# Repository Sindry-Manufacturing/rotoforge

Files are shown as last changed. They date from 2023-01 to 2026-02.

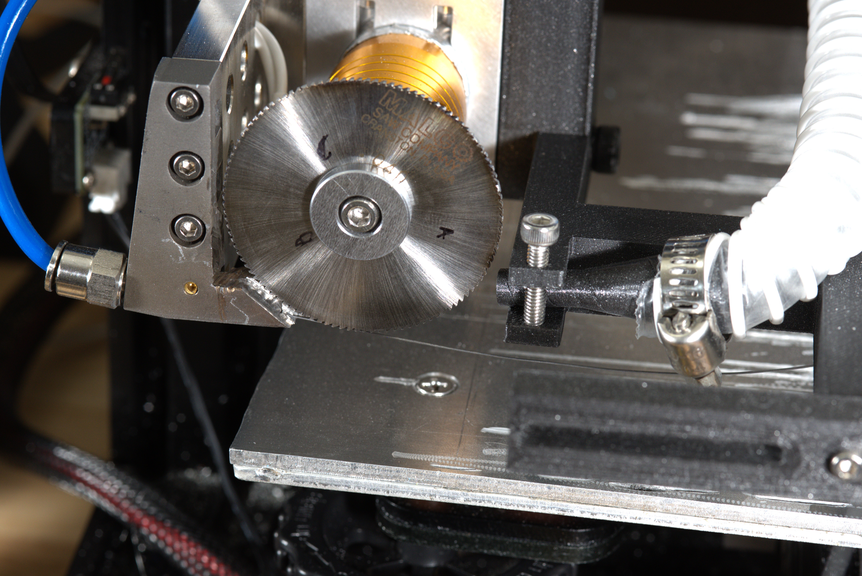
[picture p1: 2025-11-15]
docs/img/DSC_7158.jpg

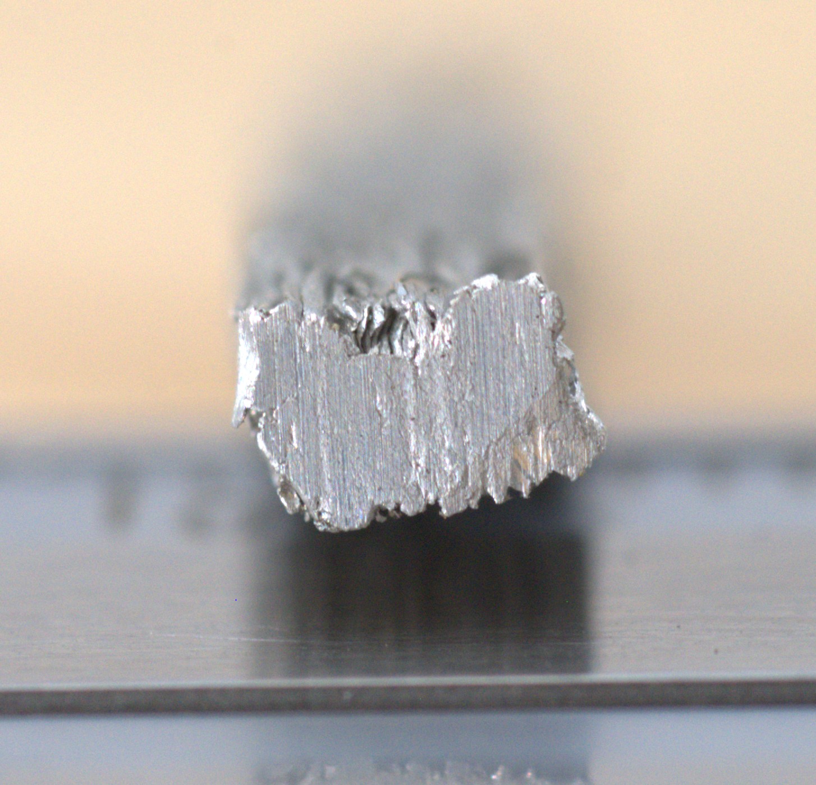
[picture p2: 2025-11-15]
docs/img/firstcleanal1100depositgroundsection.jpg

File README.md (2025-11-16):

# Rotoforge README
picture of first working iteration of Rotoforge to print a 10 mm tall wall with Al1100 wire

This is  **Rotoforge**, a 3D printer that uses continuous [friction welding](https://en.wikipedia.org/wiki/Friction_welding) to print metals, plastics and ceramics heterogeneously. 
If a wire is fed into the contact patch of a [wheel](https://en.wikipedia.org/wiki/Wheel_and_axle) which is spinning fast enough and with sufficient torque, the wire will heat up due to [friction](https://en.wikipedia.org/wiki/Friction), and become more flowable(see [thixotropy](https://en.wikipedia.org/wiki/Thixotropy)) due to plastic shear(see [flow stress](https://en.wikipedia.org/wiki/Flow_stress) and the [Zener-Hollomon Parameter](https://en.wikipedia.org/wiki/Zener%E2%80%93Hollomon_parameter)). 

Under these conditions, even materials like aluminum, copper, steel, glass, and high grade engineering plastics will become extremely fluid (without melting) and bond (given the correct contact and mixing conditions) at the contact patch, in air, without a [shield gas](https://en.wikipedia.org/wiki/Shielding_gas)!, at relatively low temperatures  and pressures. This allows relatively low force, FDM like printing of these materials on a standard 3D printer, given a way to feed wire, and a wheel with adequate speed and torque to keep the material flowing under the chosen RPM and feed rate conditions. 
This printing process, like [forging](https://en.wikipedia.org/wiki/Forging), can yield material which is stronger as printed, than the initial feedstock.  

For example, when printing with Al1100 from full soft [wire](https://www.mcmaster.com/8904k47/) (yield tensile strength (YTS) ~25 MPa, ultimate tensile strength (UTS) ~90 MPa at 100% elongation) Rotoforge achieves ~90 MPa YTS and ~120 MPa UTS at 33% elongation. a 3.6X and 1.5X improvement respectively at a modest cost in ductility. (approximate equivalent to printing ~H18 temper Al-1100)

Here is what I recommend for [getting started with Rotoforge](https://github.com/Sindry-Manufacturing/rotoforge/blob/7352ae5f737d98ba2852f8fd07662a8f5acfcd73/docs/getting_started/Getting_Started/getting_started.md)

If you would like to download the part files, schematics and documentation including text assembly tutorials and a getting started guide, clone the repository, or download the zipped folder here on github. 
We also have a [youtube channel](https://www.youtube.com/channel/UCBE1bfTLnz7WSu8h5rG6ihA) and a [read the docs page](https://www.rotoforge.com/introduction/).

If you want regular updates on progress from Michael, he has a [blog](https://dailyrotoforge.blogspot.com/) he updates periodically. 

For more active discussions we have a [discord channel](https://discord.gg/T6tJYQXE26) and a subreddit. 

for proper data storage on feeds and speeds and other printing and deposition parameters as well as in process data storage we have a [zenodo repository:](https://zenodo.org/records/10365783)

and we are occasionally active on the GOSH [community forums:](https://forum.openhardware.science/t/rotoforge-an-affordable-open-source-multimaterial-3d-printer-for-printing-metal-plastic-and-ceramics-on-the-home-desktop/4570/11)

# Files

Included in this Rotoforge repository are:
[a bill of materials](https://github.com/Sindry-Manufacturing/rotoforge/blob/5657fceeaa8cc7267cb5c8fe33cddc3ae800ea73/docs/billsofmaterials),for sourcing your own parts,

[guidelines for contributing](https://github.com/Sindry-Manufacturing/rotoforge/blob/5657fceeaa8cc7267cb5c8fe33cddc3ae800ea73/contributionguidelines.md) for those looking to be part of the community,
and 
[Documentation files](https://github.com/Sindry-Manufacturing/rotoforge/blob/5657fceeaa8cc7267cb5c8fe33cddc3ae800ea73/docs) to get the new user/developer started and provide some basic guidance for troubleshooting.

Source files, [including complete CAD data for the mechanical parts](https://github.com/Sindry-Manufacturing/rotoforge/blob/5657fceeaa8cc7267cb5c8fe33cddc3ae800ea73/src/parts/CAD), and electronics and source code to build and operate your own Rotoforge on an Ender 3 motion platform.  Principally rotoforge can be built on any motion platform, and more rigidity is better, but not strictly neccessary.
Also a [small cache of untested](https://github.com/Sindry-Manufacturing/rotoforge/blob/5657fceeaa8cc7267cb5c8fe33cddc3ae800ea73/untested%20designs) desgins in the works by other developers.

## Mechanical Parts
Rotoforge is currently just a mechanical and electronics attachment for an FDM printer which enables continuous friction welding as the new mode of energy injection and material deposition. the original mechanical CAD files are native to **Fusion360**. 
I intend to provide OpenSCAD or similar fully open source versions in the future. 

## Electronic parts
Rotoforge electronics are modeled in KiCAD and EaglePCB.  There are off the shelf versions available as well that do the job. Mostly you will need:
In the US: a 110->240 volt step up transformer.
a Variac or other method to control the speed of the flex shaft grinder (not required but useful).
A >800 watt flex shaft grinder(sometimes called a "rotary tool" or "flexshaft die grinder").

## Software
There is presently only [simple demo software for Rotoforge](https://github.com/Sindry-Manufacturing/rotoforge/blob/5657fceeaa8cc7267cb5c8fe33cddc3ae800ea73/src/afrb_playground_gui(2).py), as it runs on the motion control code and firmware of a typical FDM machine. All you will need to do to start exploring is install the mechanical and electronic parts, and use your slicer of choice (or use my provided python g-code generator) to adjust your feeds and speeds to suit the requirements of printing metals, plastics and potentially ceramics of your choice. **There is currently very little information in the wild on what feeds and speeds will work so this is a big point of ongoing exploration and where almost anyone could help!**  

## The Future
The printer only drives in straight lines in -X direction (it has to reset after every line to build thickness in Z) and can print while drifting at up to ~+-30 degree angles in the  direction right now. Typical deposition rates are 4-12 mm^3/s in this mode. But soon with the addition of a 4th axis and closed loop spindle and deposition temperature controls we will be printing ironclad boats, rocket, and car engines, robot, bicycle and car parts, at 2-4X faster in strong aluminum, copper, steel, and with your help beyond!

Rotoforge software is licensed under the [AGPL-V3](https://www.gnu.org/licenses/agpl-3.0.en.html)

Rotoforge hardware is licensed under the [CERN Open Hardware License-strong](https://cern-ohl.web.cern.ch/)

There is a video assembly guide for this printer modification [here](https://www.youtube.com/watch?v=yMjR5zOKrdI&t=20s&ab_channel=Rotoforge)
There are ongoing blogs and technical details on development of the hardware, physics and materials science involved in this project [here](https://dailyrotoforge.blogspot.com/)

## Safety
**This printer mod is LOUD and can create high speed flying debris (the wheel at full speed stores as much energy as a .357 magnum bullet). Wear eye/face/body/ear protection while the printer is in operation. If you choose not to do this, I would recommend enclosing the printer to protect you and your property and family.  If you choose to operate the printer without these safety measures, you do so at your own risk.**

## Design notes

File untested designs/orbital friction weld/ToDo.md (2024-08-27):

# To Do
- add wiring hole for motor
- add prices to BOM
- add features to mount to printer
- add large bearing in BOM
- name parts in model

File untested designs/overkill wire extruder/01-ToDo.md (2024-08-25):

# To Do
- update BOM with skrews m3 and m6
- add shaft cut list
- machin        e and test rollers

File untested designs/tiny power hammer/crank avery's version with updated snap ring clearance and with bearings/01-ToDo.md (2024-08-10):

# To Do
- update BOM with skrews
- add linear rail to BOM

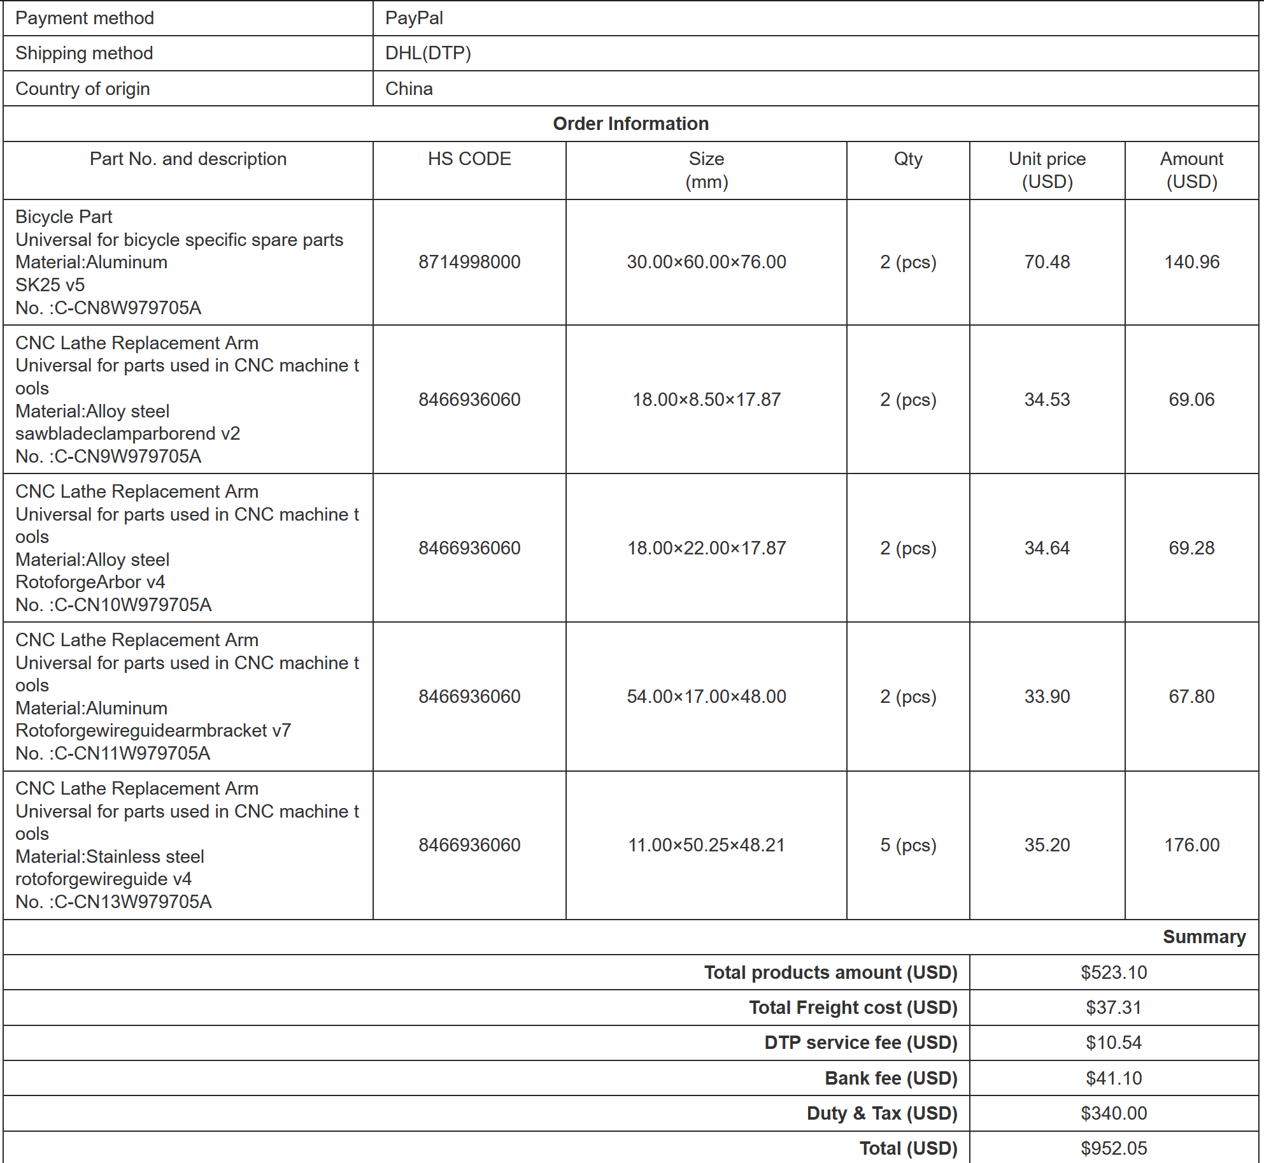
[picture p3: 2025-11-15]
docs/img/costofmechanicalpartsfromPCBway.png

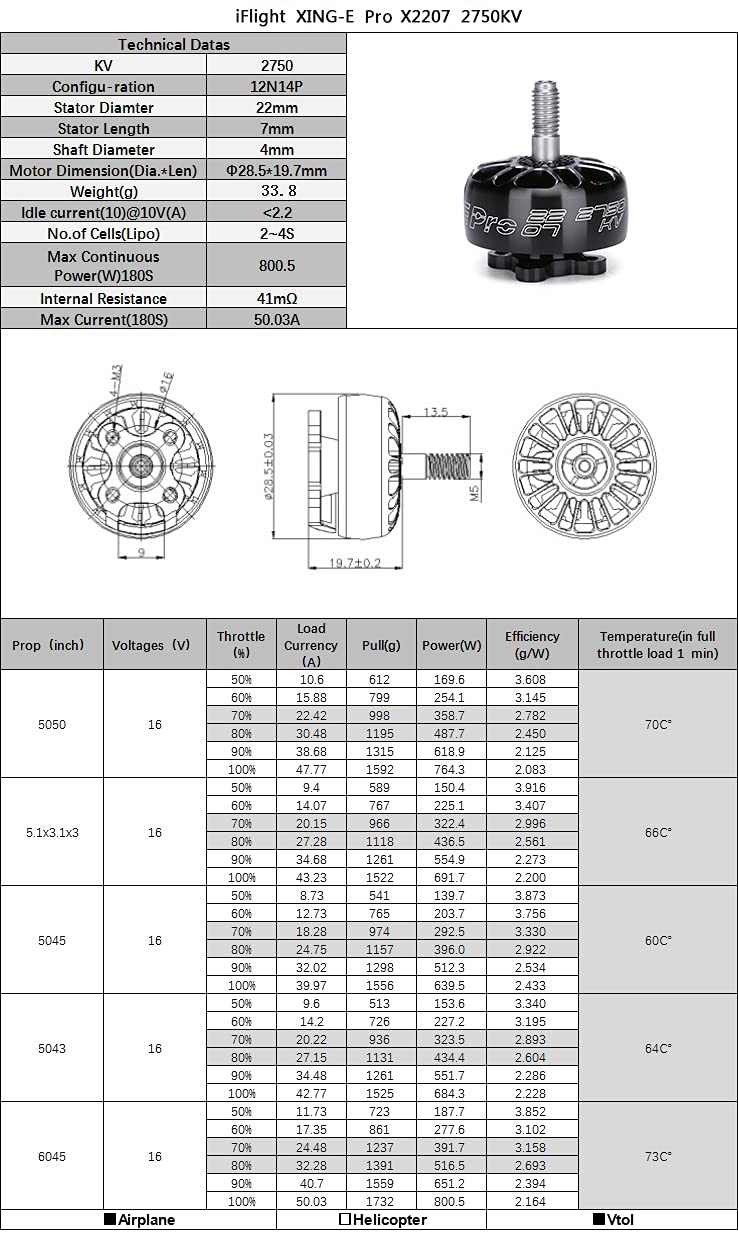
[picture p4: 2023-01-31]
src/parts/Schematics/xingEflightpro2207_.jpg

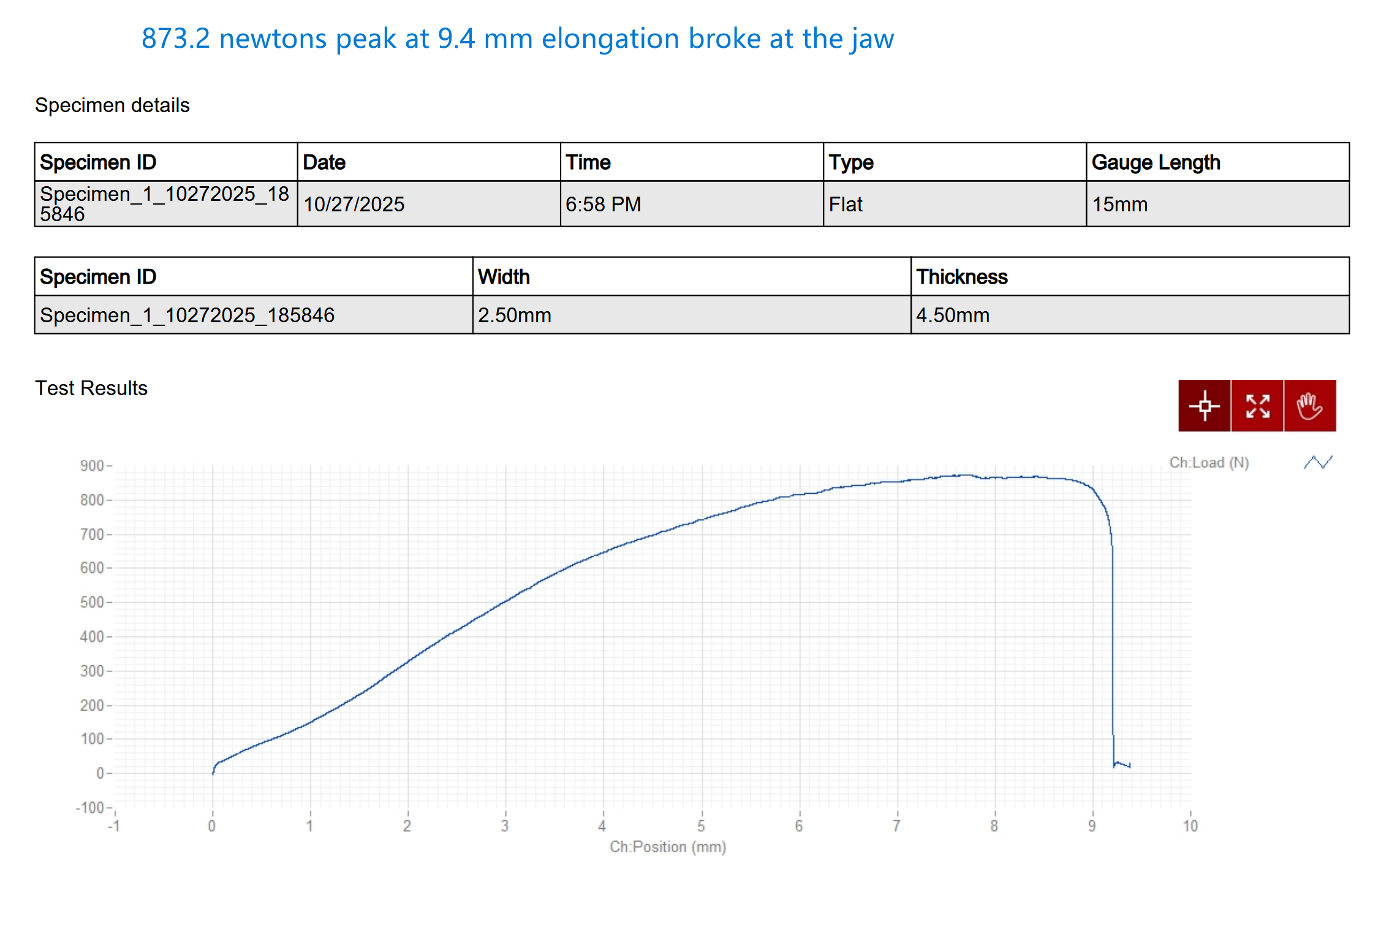
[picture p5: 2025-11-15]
docs/img/al1100asprintedtensiletest2Screenshot 2025-11-15 150118.png

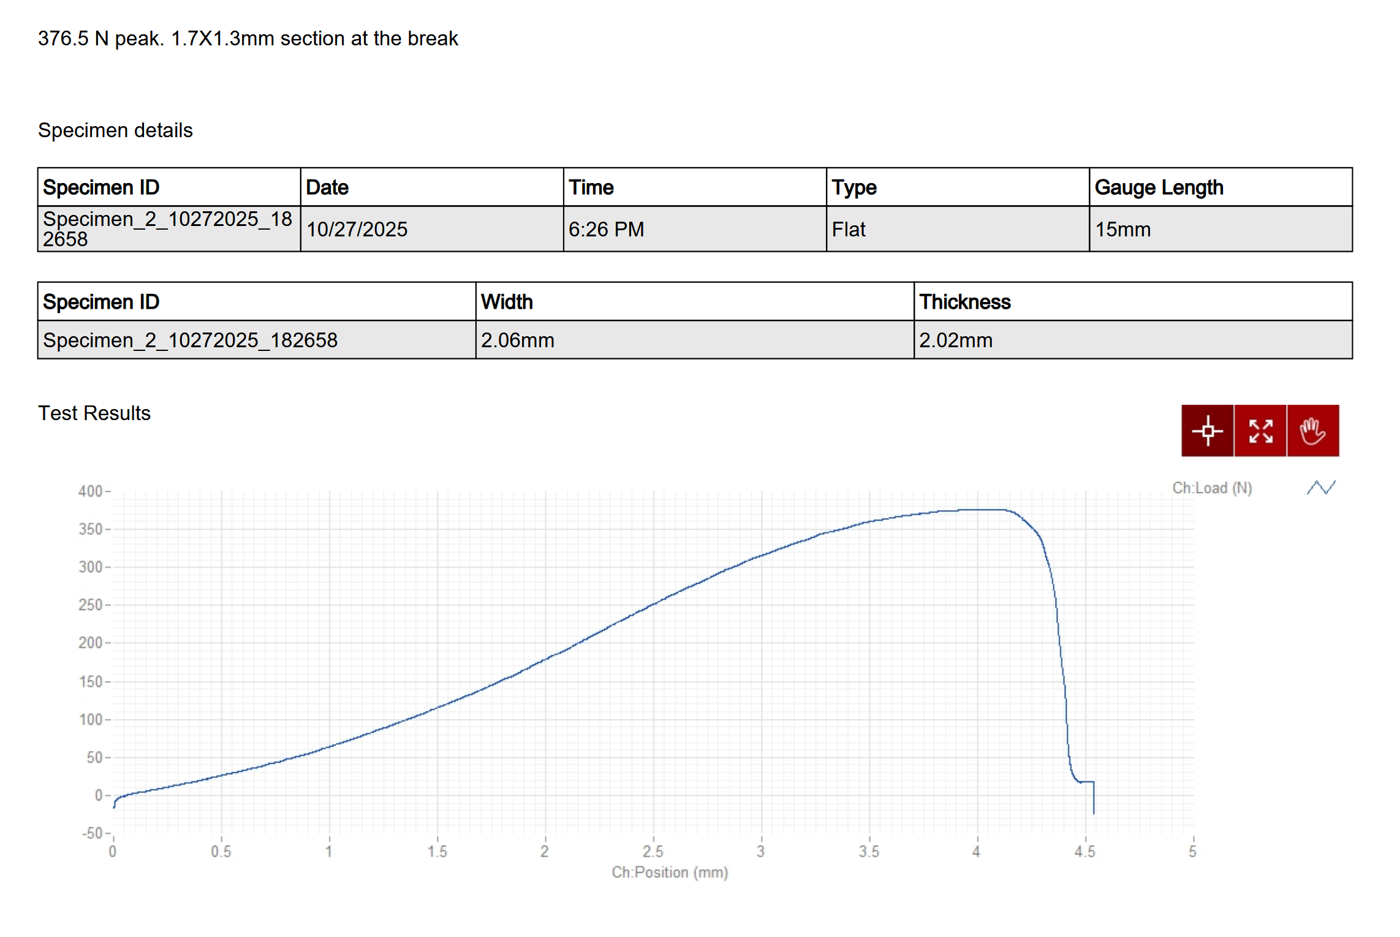
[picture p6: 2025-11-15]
docs/img/al1100asprintedtensiletest3Screenshot 2025-11-15 150118.png

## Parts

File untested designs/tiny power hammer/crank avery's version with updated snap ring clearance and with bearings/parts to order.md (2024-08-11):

2 of these: https://www.mcmaster.com/5905K526/
2 of these: https://www.mcmaster.com/98541A117/
1 of these: https://repeat-robotics.com/buy/repeat-max-brushed/
various m3 socket head cap skrews, I'm to lazy to spec all of them right now :p

what was the lienear rail again? time to fin it!

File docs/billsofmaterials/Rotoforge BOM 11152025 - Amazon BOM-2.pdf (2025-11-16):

Component | Price USD | Supplier | Link (url) | Prime? 1/0 | Comment
ender 3 | 169.99 comgrow amazonhttps://www.amazon.com/Comgrow-Creality-Ender-Aluminum-220x220x250mm/dp/B07BR3F9N6/ref=sr_1_1 | 1 reuse if you already have Modular Y Carriage Plate Upgrade | 25.99 befenbay amazonhttps://www.amazon.com/gp/product/B082ZZ9LSV/ref=ox_sc_act_title_1?smid=A3C0HXP4AGBIOG | 1 add to existing plate on ender to double thickness and improve stiffness.
Variac | 57 Yusanaga amazonhttps://www.amazon.com/gp/product/B0FCSGM2CX/ref=ox_sc_act_title_2?smid=A2Y9HFRRZJT33B | 0
110-240 V step up transformer | 69.99 Yinleader amazonhttps://www.amazon.com/gp/product/B07SZFF97X/ref=ox_sc_act_title_3?smid=A1LGU46BH79P7G | 1
1200 watt flex shaft grinder with hand piece | 79.99 Vevor amazon | https://www.amazon.com/gp/product/B0DSK8LN4Z/ref=ox_sc_act_title_4?smid=A2EWGCZPTX9ERE | 0
second Z axis screw for ender 3 | 25.99 Comgrow amazonhttps://www.amazon.com/gp/product/B07VJG4ZCG/ref=ox_sc_act_title_8?smid=A2ALB3RMNIRLH8 | 1
X axis linear rail upgrade for ender 3 | 27.99 Creality amazon https://www.amazon.com/gp/product/B0C7QJMMBW/ref=ox_sc_act_title_7?smid=A14COELW35RHNN | 1
Z axis linear rail upgrade | 52.99 Box3d amazon https://www.amazon.com/gp/product/B0BMK2V7MJ/ref=ox_sc_act_title_6?smid=A3RFW7W2S842X5 | 1
Y axis linear rail upgrade ender 3 | 52.99 box3D amazon https://www.amazon.com/gp/product/B0BMKSMBMJ/ref=ox_sc_act_title_5?smid=A3RFW7W2S842X5 | 1
1/2" arbor hole 0.02" wide HSS slitting saw blade | 17.76 Mcmaster | https://www.mcmaster.com/3044a58/ | 1 can be purchased for ~6 USD / piece from malco directly. typically lasts ~100 hours printing in aluminum.
Total USD | 580.68

you will need to print a wire spool holder and some way to hang or otherwise support the grinder motor.
You may also want to enclose the printer, as it tends to be quite noisy, like a table saw. it also produces some swarf and debris as in grinding or sawing. if you use this printer unenclosed you do so at your own risk and should wear adequate hearing and eye/face/body protection while it is in operation. Custom Parts (PCBWayPrices)
SK 25 spindle holder for flex shafthandpiece | 70.48 | https://github.com/Sindry-Manufacturing/rotoforge/blob/5657fceeaa8cc7267cb5c8fe33cddc3ae800ea73/src/parts/CAD/SK25%20v7.step
Arbor clamp for Saw blade | 34.53 | https://github.com/Sindry-Manufacturing/rotoforge/blob/5657fceeaa8cc7267cb5c8fe33cddc3ae800ea73/src/parts/CAD/sawbladeclamparborend%20v2.step Rotoforge 6mm shaft X 1/2" arbor for saw blades | 36.64 | https://github.com/Sindry-Manufacturing/rotoforge/blob/5657fceeaa8cc7267cb5c8fe33cddc3ae800ea73/src/parts/CAD/RotoforgeArbor%20v4.step Rotoforge wire guide arm bracket for supporting wire guide | 33.9 | https://github.com/Sindry-Manufacturing/rotoforge/blob/5657fceeaa8cc7267cb5c8fe33cddc3ae800ea73/src/parts/CAD/Rotoforgewireguidearmbracket%20v12.step Wire guide shoe | 35.2 | https://github.com/Sindry-Manufacturing/rotoforge/blob/5657fceeaa8cc7267cb5c8fe33cddc3ae800ea73/src/parts/CAD/rotoforgewireguide%20v11.step
Total USD | 210.75
Total Mod Cost: | 791.43

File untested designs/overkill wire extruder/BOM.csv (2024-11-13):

Part name | Part Link | Number Needed | price:
Bearing | https://www.amazon.com/MR106-2RS-Precision-Bearing-6x10x3mm-Bearings/dp/B08TBT45J3 | 1 | 11.99
Roll Pin | https://www.mcmaster.com/97161A116/ | 1 pack | 14.28
Teflin tube | https://www.mcmaster.com/5239K23/ | 10 ft | 14.20
motor with gearbox | https://www.omc-stepperonline.com/nema-11-stepper-motor-bipolar-l-51mm-w-gear-ratio-27-1-planetary-gearbox-11hs20-0674s-pg27 | 1 | 36.54
m3 socket head cap skrews | not gonna find rn | various lenghths
6mm shaft | https://www.mcmaster.com/4143N11/ | 1 | 8.70

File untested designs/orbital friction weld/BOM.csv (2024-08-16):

name | link | number | price
bearing1 | https://www.mcmaster.com/7804K115/ | 2 | 8.37
motor | https://shop.iflight.com/xing-x2814-fpv-nextgen-motor-pro838 | 1 | 38.99
feed wire | https://www.amazon.com/5356-Aluminum-Welding-ER5356-1-030/dp/B07N99KK6M?th=1 | 1 | $14
stock for shaft | https://www.mcmaster.com/89535K87/ | 6 in
long drill for shaft | https://www.mcmaster.com/8934A15/ | 2 cause break easy
tube 1 | https://www.onlinemetals.com/en/buy/brass/0-0625-od-x-0-014-wall-round-brass-tube-260-272-12-long-%283-pieces%29/pid/mp-00000820
tube 2 | https://www.onlinemetals.com/en/buy/brass/0-09375-od-x-0-014-wall-round-brass-tube-260-272-12-long-%283-pieces%29/pid/mp-00000868
tube 3 | https://www.onlinemetals.com/en/buy/aluminum/0-125-od-x-0-014-wall-round-aluminum-tube-3003-h14-12-long-%283-pieces%29/pid/mp-00000723

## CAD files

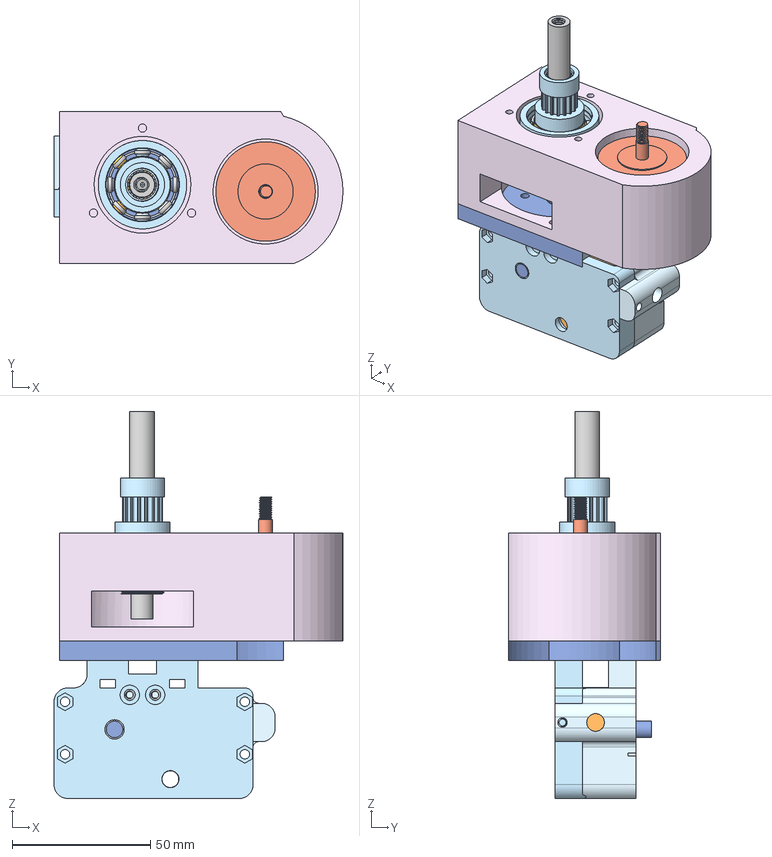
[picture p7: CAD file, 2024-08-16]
untested designs/orbital friction weld/Orbital Friction Full Assy.step
104.5 x 55.0 x 140.0 mm
extruderbody
driveroller
extruder brace
tension bracket
tensioningrooler
Spur gear (20 teeth) x 2
wire support
plate
5972K358_Ball Bearing x 11
7487N34_Precision Stainless Steel Ball Bearing x 52
frame

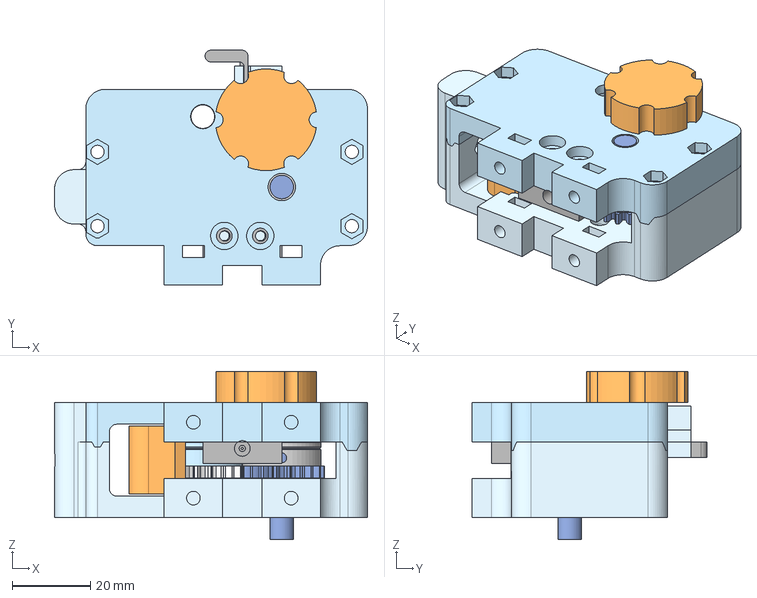
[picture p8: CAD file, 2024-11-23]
untested designs/overkill wire extruder/Overkill Extruder- AP242.step
80.0 x 60.0 x 43.0 mm

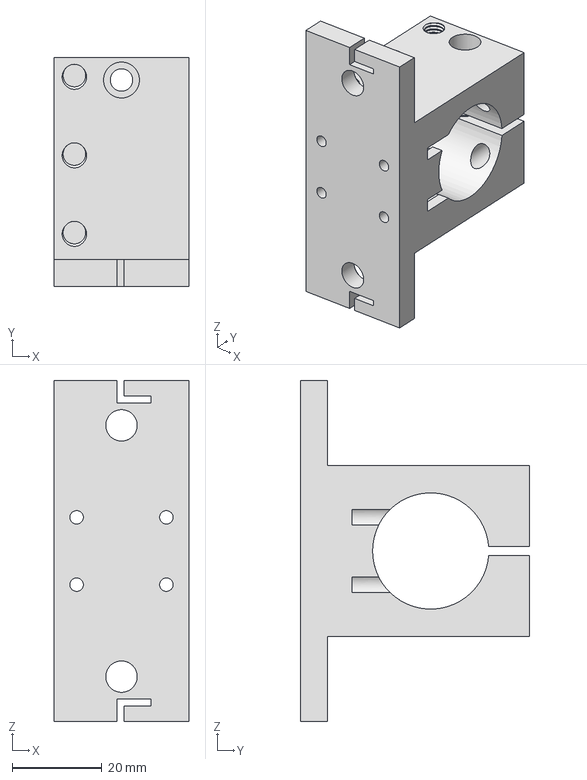
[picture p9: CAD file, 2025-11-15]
src/parts/CAD/SK25 v7.step
30.0 x 51.0 x 76.0 mm

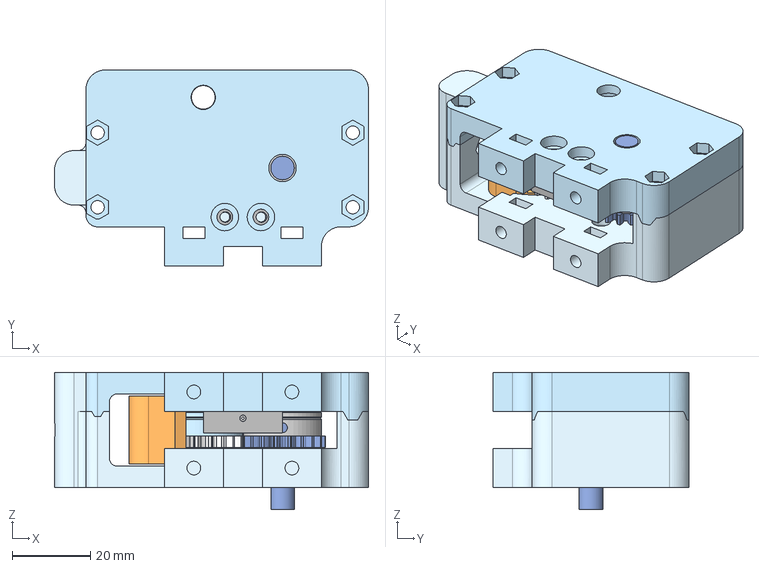
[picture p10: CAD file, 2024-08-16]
untested designs/overkill wire extruder/Overkill Extruder v4.step
80.0 x 50.0 x 35.0 mm

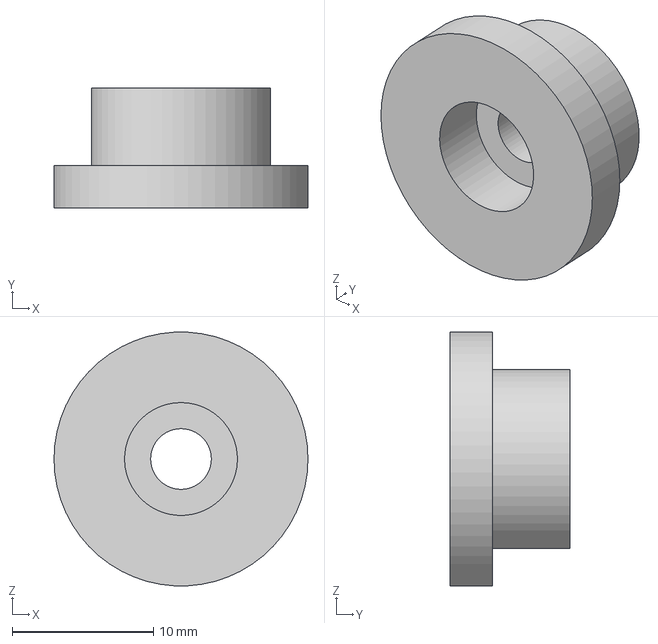
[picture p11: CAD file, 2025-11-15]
src/parts/CAD/sawbladeclamparborend v2.step
18.0 x 8.50 x 18.0 mm

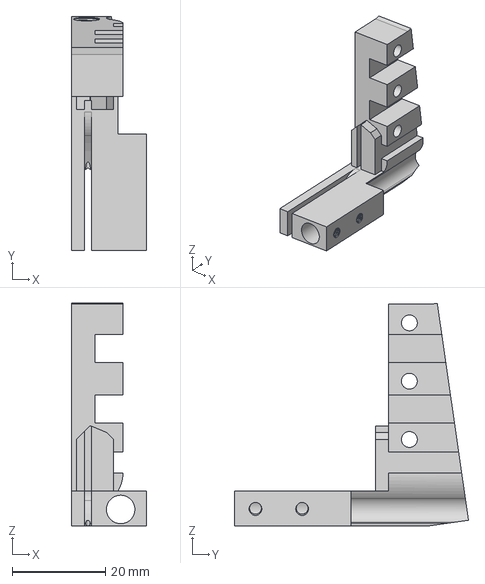
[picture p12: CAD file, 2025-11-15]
src/parts/CAD/rotoforgewireguide v13.step
16.0 x 50.2 x 47.7 mm

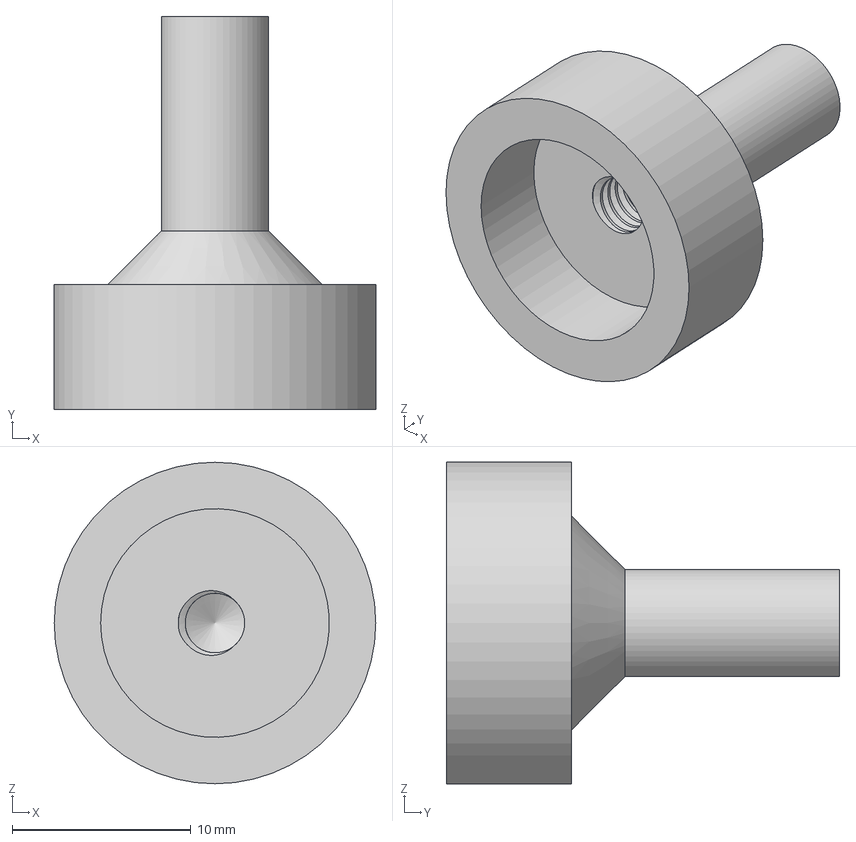
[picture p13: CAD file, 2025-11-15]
src/parts/CAD/RotoforgeArbor v4.step
18.0 x 22.0 x 18.0 mm

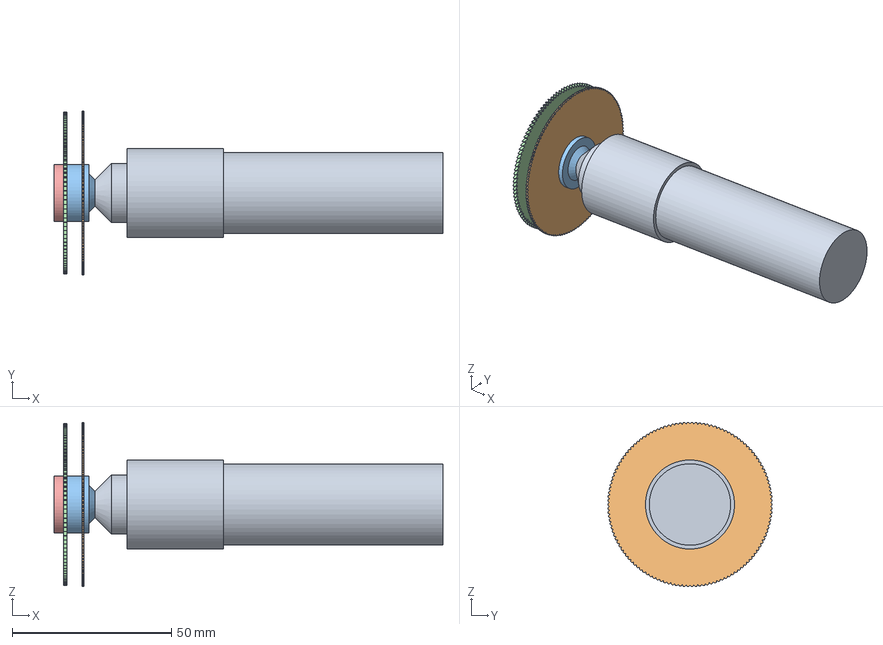
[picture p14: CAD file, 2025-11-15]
src/parts/CAD/standinrotoforgespindle v5.step
122.3 x 51.7 x 51.7 mm
roughgeometricplaceholderrotarygrinder
RotoforgewheelV9
RotoforgeArbor
3044A65_Smooth-Finish Slitting Saw
sawbladeclamparborend

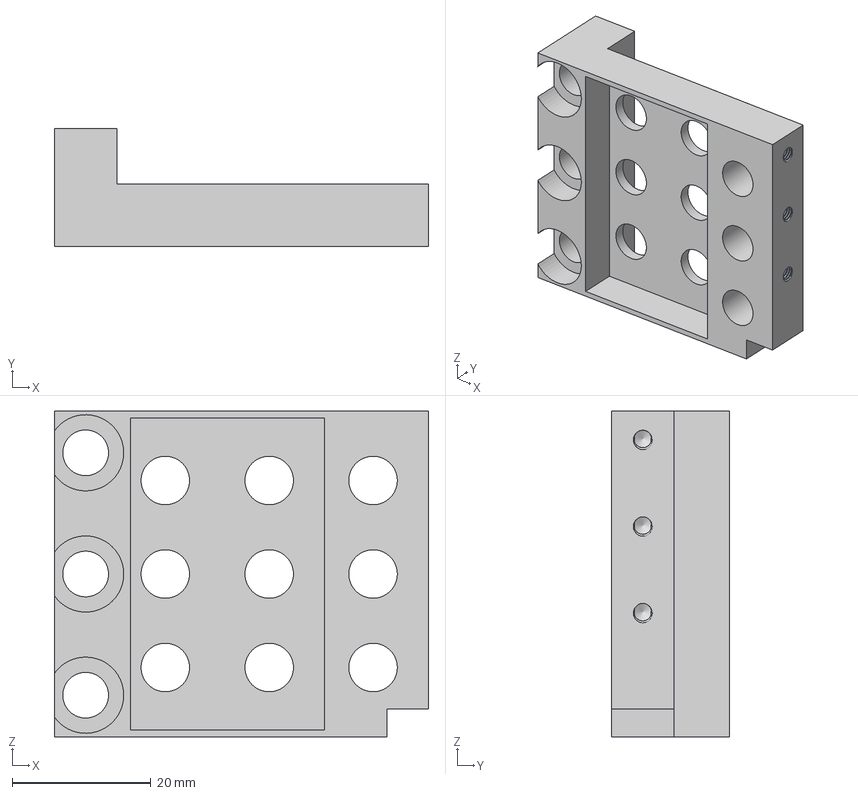
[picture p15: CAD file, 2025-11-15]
src/parts/CAD/Rotoforgewireguidearmbracket v12.step
54.0 x 17.0 x 47.0 mm

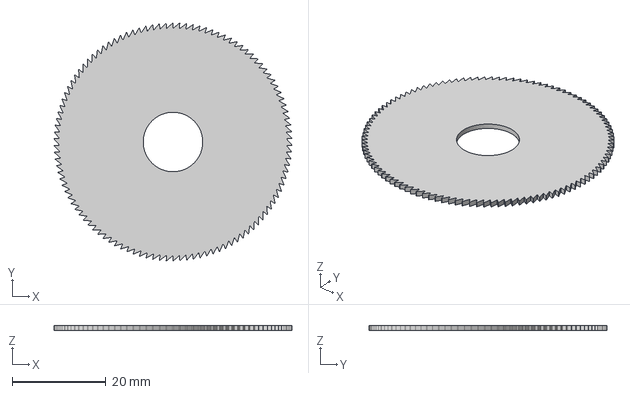
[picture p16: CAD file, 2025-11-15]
src/parts/CAD/3044A65_Smooth-Finish Slitting Saw v1.step
50.8 x 50.8 x 1.02 mm

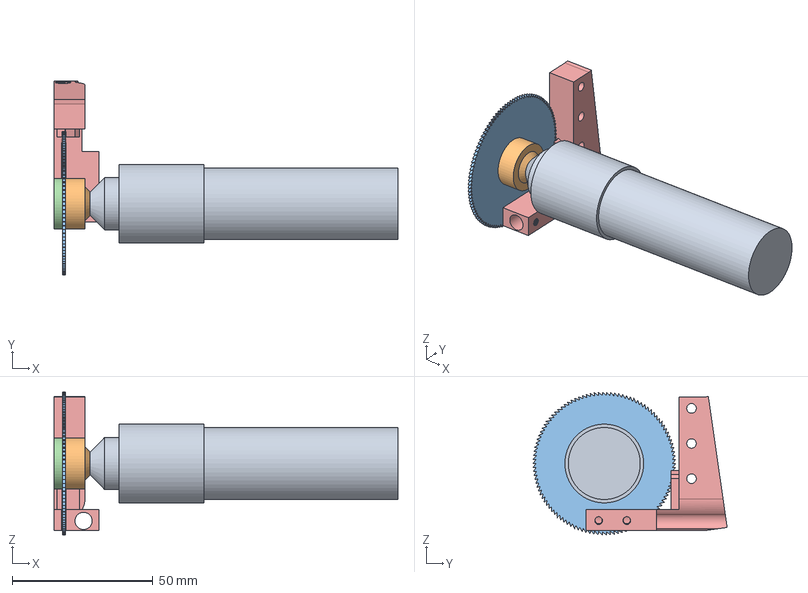
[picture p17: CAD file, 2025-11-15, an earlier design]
src/parts/CAD/rotoforgewireguide v11.step
122.3 x 69.1 x 50.8 mm
roughgeometricplaceholderrotarygrinder
RotoforgeArbor
3044A65_Smooth-Finish Slitting Saw
sawbladeclamparborend

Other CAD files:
src/parts/Schematics/rotoforgeender3mount Drawing v1.dwg
src/parts/CAD/3044A65_Smooth-Finish Slitting Saw v1.f3d
src/parts/CAD/RotoforgeArbor v4.f3d
src/parts/CAD/Rotoforgewireguidearmbracket v12.f3d
src/parts/CAD/SK25 v7.f3d
src/parts/CAD/rotoforgewireguide v13.f3z
src/parts/CAD/sawbladeclamparborend v2.f3d

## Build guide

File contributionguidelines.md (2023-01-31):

#Guidelines for contributing
Below is essentially a clone of the mozilla developer code of conduct... we generally adhere to this structure of dealing with each other. 
Communications regarding contribution and community rules can be provided via the discord, comments on the youtube channel, posts on the subreddit, or via discussions on github.

# Contributor Covenant Code of Conduct

## Our Pledge

We as members, contributors, and leaders pledge to make participation in our
community a harassment-free experience for everyone, regardless of age, body
size, visible or invisible disability, ethnicity, sex characteristics, gender
identity and expression, level of experience, education, socio-economic status,
nationality, personal appearance, race, caste, color, religion, or sexual
identity and orientation.

We pledge to act and interact in ways that contribute to an open, welcoming,
diverse, inclusive, and healthy community.

## Our Standards

Examples of behavior that contributes to a positive environment for our
community include:

* Demonstrating empathy and kindness toward other people
* Being respectful of differing opinions, viewpoints, and experiences
* Giving and gracefully accepting constructive feedback
* Accepting responsibility and apologizing to those affected by our mistakes,
  and learning from the experience
* Focusing on what is best not just for us as individuals, but for the overall
  community

Examples of unacceptable behavior include:

* The use of sexualized language or imagery, and sexual attention or advances of
  any kind
* Trolling, insulting or derogatory comments, and personal or political attacks
* Public or private harassment
* Publishing others' private information, such as a physical or email address,
  without their explicit permission
* Other conduct which could reasonably be considered inappropriate in a
  professional setting

## Enforcement Responsibilities

Community leaders are responsible for clarifying and enforcing our standards of
acceptable behavior and will take appropriate and fair corrective action in
response to any behavior that they deem inappropriate, threatening, offensive,
or harmful.

Community leaders have the right and responsibility to remove, edit, or reject
comments, commits, code, wiki edits, issues, and other contributions that are
not aligned to this Code of Conduct, and will communicate reasons for moderation
decisions when appropriate.

## Scope

This Code of Conduct applies within all community spaces, and also applies when
an individual is officially representing the community in public spaces.
Examples of representing our community include using an official e-mail address,
posting via an official social media account, or acting as an appointed
representative at an online or offline event.

## Enforcement

Instances of abusive, harassing, or otherwise unacceptable behavior may be
reported to the community leaders responsible for enforcement at
[INSERT CONTACT METHOD].
All complaints will be reviewed and investigated promptly and fairly.

All community leaders are obligated to respect the privacy and security of the
reporter of any incident.

## Enforcement Guidelines

Community leaders will follow these Community Impact Guidelines in determining
the consequences for any action they deem in violation of this Code of Conduct:

### 1. Correction

**Community Impact**: Use of inappropriate language or other behavior deemed
unprofessional or unwelcome in the community.

**Consequence**: A private, written warning from community leaders, providing
clarity around the nature of the violation and an explanation of why the
behavior was inappropriate. A public apology may be requested.

### 2. Warning

**Community Impact**: A violation through a single incident or series of
actions.

**Consequence**: A warning with consequences for continued behavior. No
interaction with the people involved, including unsolicited interaction with
those enforcing the Code of Conduct, for a specified period of time. This
includes avoiding interactions in community spaces as well as external channels
like social media. Violating these terms may lead to a temporary or permanent
ban.

### 3. Temporary Ban

**Community Impact**: A serious violation of community standards, including
sustained inappropriate behavior.

**Consequence**: A temporary ban from any sort of interaction or public
communication with the community for a specified period of time. No public or
private interaction with the people involved, including unsolicited interaction
with those enforcing the Code of Conduct, is allowed during this period.
Violating these terms may lead to a permanent ban.

### 4. Permanent Ban

**Community Impact**: Demonstrating a pattern of violation of community
standards, including sustained inappropriate behavior, harassment of an
individual, or aggression toward or disparagement of classes of individuals.

**Consequence**: A permanent ban from any sort of public interaction within the
community.

## Attribution

This Code of Conduct is adapted from the [Contributor Covenant][homepage],
version 2.1, available at
[https://www.contributor-covenant.org/version/2/1/code_of_conduct.html][v2.1].

Community Impact Guidelines were inspired by
[Mozilla's code of conduct enforcement ladder][Mozilla CoC].

For answers to common questions about this code of conduct, see the FAQ at
[https://www.contributor-covenant.org/faq][FAQ]. Translations are available at
[https://www.contributor-covenant.org/translations][translations].

[homepage]: https://www.contributor-covenant.org
[v2.1]: https://www.contributor-covenant.org/version/2/1/code_of_conduct.html
[Mozilla CoC]: https://github.com/mozilla/diversity
[FAQ]: https://www.contributor-covenant.org/faq
[translations]: https://www.contributor-covenant.org/translations

#Opportunities for development 

Hardware Opportunities for Development:
**higher power density lighter weight BLDC motor with a hollow shaft made of or internally coated with some hard materials extremely resistant to high temperature(above 1300 K) extremely resistant to abrasion at over 35K RPM, and extremely resistant to wetting and welding with metals like aluminum, copper, titanium and stainless steel.** 
**cheap but high rigidity motion platform like the ender 3 but with a stiffer gantry axis and comparable cost.** 

Electronic Opportunities for development:
**A dedicated all in one, tunable power converter of ~200 watt capability, with an integrated ESC and PWM controller interface for manual tuning and connection to existing PWM control signals available on 3D printer control boards would be of value here...**

Software opportunities for developemnt: 
**TLDR; Rotoforge enables much better closed loop sensing and control of the material printing process and could enable fully automated heterogeneous material manufacturing with appropriate software developemnt.**

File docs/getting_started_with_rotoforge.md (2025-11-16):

# How to build a rotoforge
1. download the repo
2. open the [bill of materials](https://github.com/Sindry-Manufacturing/rotoforge/blob/29fc23453d98a2a53141974132ee8f29831c75b1/docs/billsofmaterials/Rotoforge%20BOM%2011152025.ods) (BOM) in the billsofmaterials directory 
3. source the parts you can buy, build/have built the small number of custom parts (or print them)
4. assemble the parts
5. start printing and [experimenting](https://github.com/Sindry-Manufacturing/rotoforge/blob/29fc23453d98a2a53141974132ee8f29831c75b1/docs/getting_started_afrbplayground.md). Get started faster with my [afrb playground script](https://github.com/Sindry-Manufacturing/rotoforge/blob/29fc23453d98a2a53141974132ee8f29831c75b1/src/afrb_playground_gui(2).py)
6. Share what you learn with all of us on [Discord](https://discord.gg/T6tJYQXE26) 

Wondering how you can help? 

# Ways you could help the project

1. **4th-5th-6th axis** for certainty and better precision for curvy shapes

2. **better designs** for wire guide shoes, that can work(not stick to the wire, do a reasonable job of preventing clogging of the wire guide, prevent wire buckling as it is fed into the wheel, heat the wire up to ~600 C at least) 

3. **slicer mods** (custom slicer? or something) that respects the particular requirements of the wheel and leverages the unique properties of metal and the wheel process to make parts in ways that may not be exactly like FDM. and will probably have some advantages and disadvantages comparatively.  i got GPT to get a probably pretty bad start on it that produces results that look reasonable but maybe are not totally printable yet. There are few if any safety checks for printability, though the generally requirements of printing with the wheel appear to be respected. 

4. **closing the loop on the wheel itself.** 
I am currently running everything open loop like a caveman. Controlling velocity/torque/position control on the wheel could all be useful (in addition to temperature) to tell us more about what is actually happening at the deposition zone. (which would be a matter of broad research/general user/commercial interest beyond just printing single alloys)
I am currently planning to obtain a high speed camera(probably a chronos or similar) to really look closely at what is happening (get some glory shots) and try to connect the effects we can see with motor control conditions and operating points. Trying to do a better job of mapping the whole printing parameter space as much as I can... this is a huge lift and will take a long time on my own...but I think will be well worth the money and time to speed up slicing parameter development and familiarizing (myself) people with the concept and how it works....if anyone ends up implementing a spindle on head approach or otherwise using a BLDC that would benefit from such control it would be  of great service. 

I think if we want to go for smaller wheels, or higher wheel speeds (60-100K RPM) to get process forces even lower, further increase deposition rates, and allow for finer features, this is going to be an important step that I initially started on by then tried to simplify away with the big brushed DC motor die grinder currently on my prototype. I accepted the lower speed and 50 mm diameter  wheel to be able to prove function. 
the move to software controlled closed loop high speed BLDC drive is going to be a significant challenge and involves to many steps for me to tackle simultaneously. But if someone else wants to give it a try that would be awesome. 

5. **build implementations of the same basic concept**....others building roll bonders would be incredibly helpful, because then the onus is not always on me to be iterating the hardware and we can get more perspective on how to make it physically better and simplify the design to its most essential elements. I would consider this project a success when we can take the printer we have designed, throw it to a random joe in a remote (but electricity having) corner of the amazon rainforest, and have them be able to use it make something of use to them. Like a tool, or replacement part for a motor bike or car, or some structural part for their homes/businesses. 

6. **Help with planning, documenting, and thinking about what the future of the project looks like** where do people want to see this go? would anyone buy this if it looked like a product? maybe it should be more like a voron style thing?  I have my own ideas about what I want it to be, but I need more perspective to make informed decisions about how to organize things when we stat to get more serious with the system and push it beyond just working proof of concept.

7. **building local feedstock production**....wires of the diameters we need are not easy to find at affordable prices in small quantities for every alloy. 
right now we are basically limited to naval brass, 510 bronze, pure copper, al1100, mild carbon steel, 1080 spring steel, 304/316stainless steel, 5054 aluminum and a few others in the (24 AWG) ~0.5mm and smaller diameter we require. Basically what can be ordered small batch from china or elsewhere. 

A small bench top and low power electric and mostly automatic (reasonably reliable(90% uptime for 24/7 operation) wire drawing system that can take larger diameter wires (up to ~3mm rod perhaps) and draw it down to 0.5mm or smaller and spool that wire onto a roll (perhaps annealing in line to relax the stress of drawing) would be extremely helpful. (more than tripling our available feed stock options) 

I intend to do this myself eventually, and try for as much vertical integration as possible if that is what must be done to see this technology made manifest. 

8. **Documentation help** someone with the time, will, energy and know how to keep track of what is going on here in the discord and elsewhere, and document the goings on in a broader externally accessible, permanently linkable and indexable wiki or similar such thing. I am not a web admin or web designer, and while the task is easier than it ever has been with an LLM the job of managing that system is itself a bit too much for me to do continuously. I mostly operate by making all at once updates condensed from my aggregated notes, discord posts, and personal video logs/ writings each time I make a video, then I update the github and Mkdocs to reflect those changes (ideally in reverse order)....This is obviously a very poor way to do things and would benefit from a more skilled and consistent hand.

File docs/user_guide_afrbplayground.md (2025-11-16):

# afrb Playground — Operator & Developer Getting Started Guide
*(for RotoForge / additive friction roll bonding hardware)*

This GUI script generates simple, test‑friendly G‑code patterns (lines, dots, rasters, drifts, overhang tests) for wire‑fed friction roll bonding. It’s not a full slicer—think of it as a safe, inspectable pattern generator you can extend.

The script is in development and very quick and dirty. you have been warned.
---

## Part A — New users (operators)

### What the tool does
- Builds G‑code with a standard header (units, homing, optional bed preheat & wait, fan, spindle spin‑up) and a matching footer (stop spindle/fan, safe Z). It then prints one of five pattern types from a tab.
- Defaults are provided per material (Al 1100‑O Ø0.50 mm, Steel 1008 Ø0.356 mm). You can override everything.

**Units:** distances in mm, feeds **F** in mm/min, temperature in °C, time in ms. Extrusion **E** is *relative* (M83), and the script frequently resets E (G92 E0).

---

### Quick start: first bonded wall (Aluminum, single track)
1. **Preset:** **Aluminum 1100‑O (Ø0.50 mm)** (typical: Deposition F≈1000, Fan=255, Spindle=30000, Bed≈110 °C, Dwell=2000 ms).
2. **(Optional) Bed preheat:** Set **Bed °C**, keep **Wait (M190)** checked, and **Dwell ms ~2000**.
3. **Straight / Multitrack** tab: 60 mm line, **Z 0.8 → 10.0**, **Layer 0.10** in −X. Use **Extrusion Mode = “x”** to start, or **“volume”** for area‑matched feed.
4. **Generate G‑code…** Save, transfer to the controller, set safe zeros, and run. (For a dry run, set **Spindle=0** and **Bed=0**.)

   I have had best results using pronterface. but other g-code senders should work as well. It is not generally neccessary to heat the bed but this can reduce forces and make thicker layerheights possible. 
   You will also need to reset the starting Z based on your particular printer and print bed height / leveling /homing setup. I have not included provisions for automatic bed leveling probes consciously. 

---

### UI map

**Top bar**
- **Material Preset / Toggle** — aluminum or steel presets (also set bed defaults).
- **Bed °C / Wait (M190) / Dwell ms** — optional preheat+wait+dwell; Bed 0 disables heat.

**Tabs (pattern types)**
1) **Straight / Multitrack** — straight beads with optional multitrack(lines side by side to make thicker walls/perimeters) & overlap.  
2) **Dot Stack** — “pulsed” dots stacked in Z at fixed XY.  
3) **Sideways Micro‑Raster** — short −X strokes stepped in Y to fill a patch.  
4) **Diagonal Drift** — segmented −X line that drifts in +Y.  
5) **Overhang Tests** — −X lines at varying Z/Y offsets.

---

### Parameter quick‑reference

**Common**: `feed_travel`, `feed_z`, `feed_dep`, `spindle`, `fan`, `travel_z`, `dwell_ms`, `runout`, `retract`, `bed_temp`, `wait_bed`, `bed_dwell_ms`.

**Extrusion**:
- `x` → 1 E/mm (simple).
- `volume` → `(bead_width × layer_height) / wire_area`, `wire_area = π (wire_diam/2)^2`.

**Straight / Multitrack**: Start X/Y; **Path Length X (−X)**; Z start/step/final; `e_mode`, `bead_width`, `wire_diam`; `lead_in`, `runout`, `retract`, optional `Z‑dive cut`; Multitrack: `track_count`, `overlap_frac`, `serpentine_y`.

**Dot Stack**: X/Y fixed; Z start/step/final; `e_pulse`, `e_retract`.

**Sideways Micro‑Raster**: Start X/Y; `x_stroke` (−X), `y_span`, `dy_step`; Z start/step/final; `e_mode`, `bead_width`, `wire_diam`; `runout`, `retract`.

**Diagonal Drift**: Start X/Y; `x_total` (−X), `y_drift`, `seg_dx`; Z start/step/final; `e_mode`, `bead_width`, `wire_diam`; `runout`, `retract`.

**Overhang Tests**: Start X, Base Y; `length_x` (−X); `z_first`; `z_offsets_csv`; `y_offsets_csv` or `y_step`; `e_mode`, `bead_width`, `layer_height`, `wire_diam`; feeds; `runout`, `retract`.

---

### Two simple recipes
- **Tall straight wall:** `track_count=1`, `z_step=0.10`, `z_final≈10`, `e_mode="x"`, `runout=2`, `retract=2`.  
- **Small filled patch:** `x_stroke=5`, `y_span=6`, `dy_step≈0.33`, 2–4 layers, `runout=1`, `retract=2`.

---

## Part B — Developers

### Code layout
- Helpers: `parse_csv_floats`, `compute_e_per_mm`, `gcode_header`, `gcode_footer`.
- Patterns: `gen_straight_multitrack`, `gen_dot_stack`, `gen_sideways_micro_raster`, `gen_diagonal_drift`, `gen_overhang_tests`.
- GUI: `Playground` builds the top bar and five tabs; `_common_params()` centralizes shared defaults; `_ent(...)` makes labeled entries; `_gen_*` handlers gather → generate → save.

### Add a new pattern
```python
def gen_my_pattern(P):
    lines = []
    lines += gcode_header(P)
    # ... your moves here ...
    lines += gcode_footer(P)
    return "\n".join(lines)

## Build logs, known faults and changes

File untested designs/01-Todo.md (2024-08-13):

# To Do
- add twisty back and fourthey design
- make adapter for that mount to papalio extruder used elsewhere

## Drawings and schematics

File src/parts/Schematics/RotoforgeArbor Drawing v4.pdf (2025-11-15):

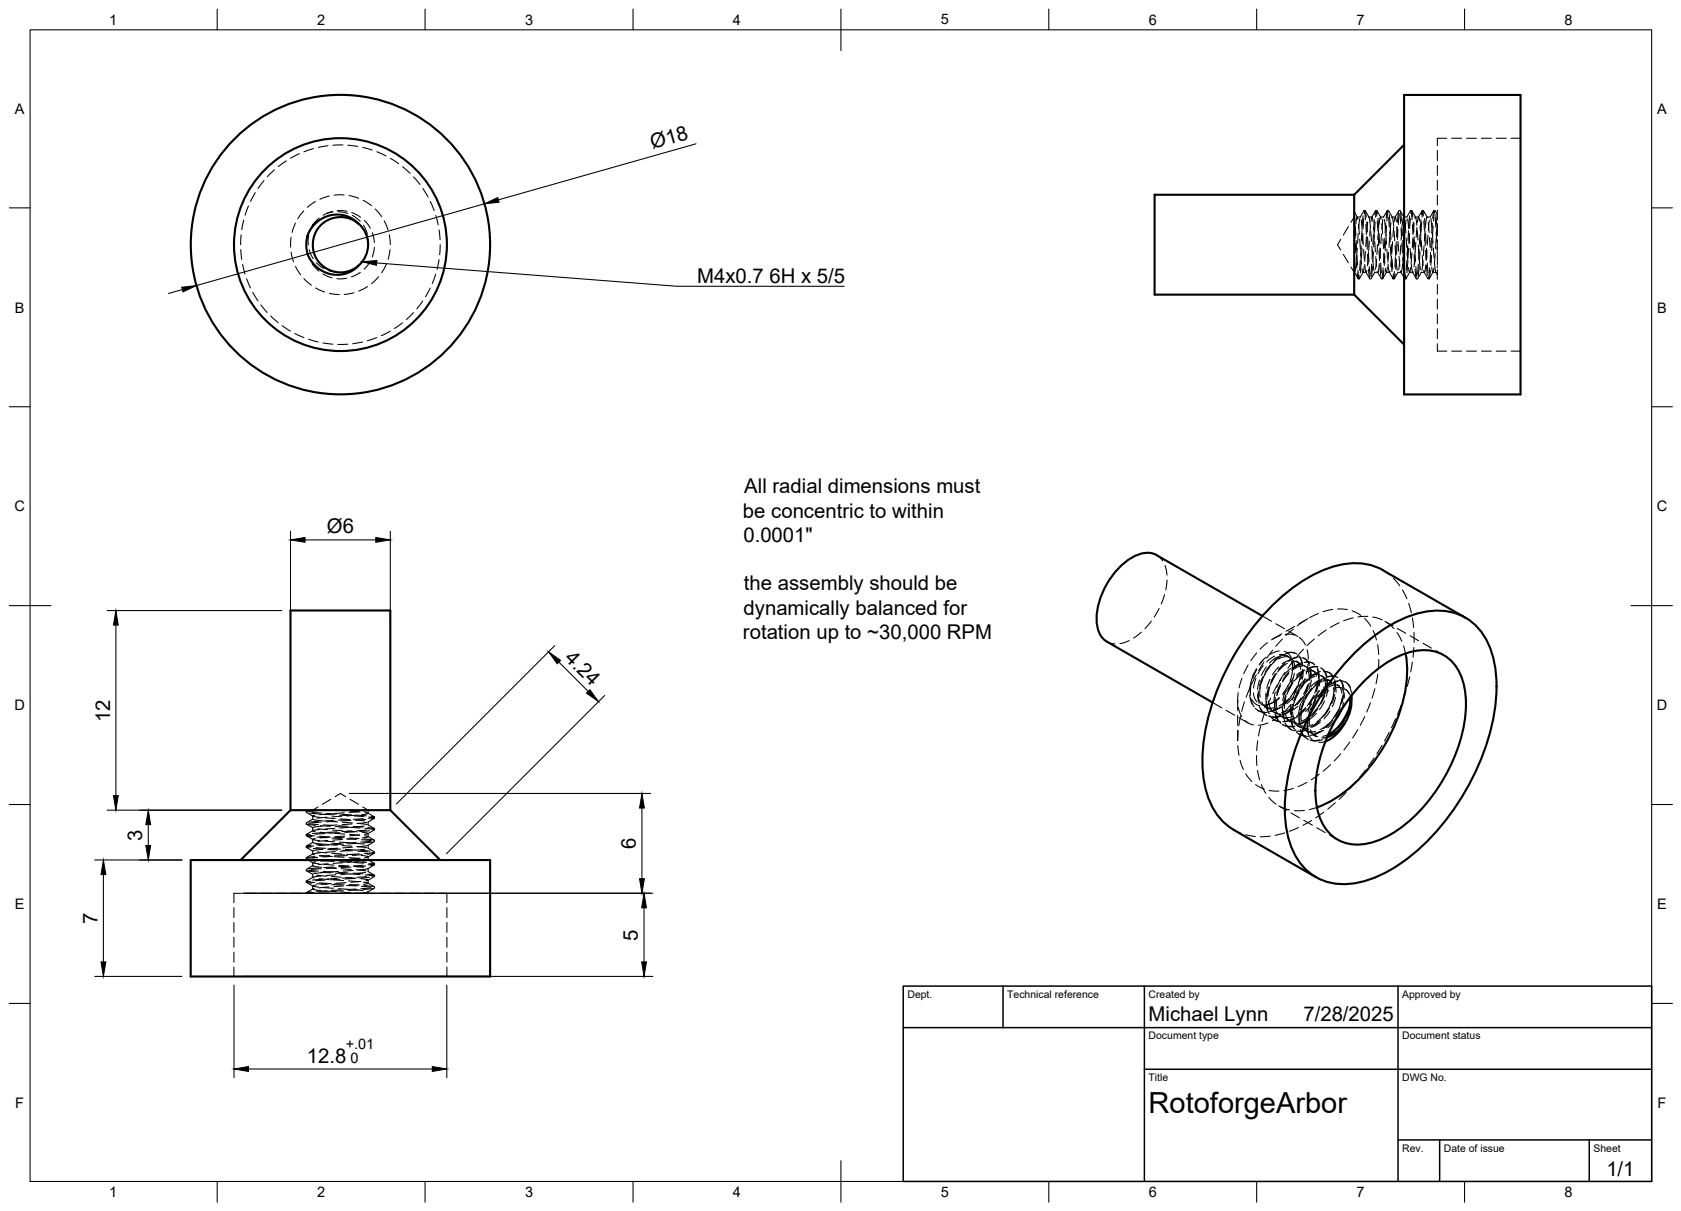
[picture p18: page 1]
Title; DWG No.; Rev.; Date of issue; Sheet

All radial dimensions must
be concentric to within

the assembly should be
dynamically balanced for
rotation up to ~30,000 RPM

Dept. | Technical reference | Created by Michael Lynn 7/28/2025 | Approved by

Document type | Document status

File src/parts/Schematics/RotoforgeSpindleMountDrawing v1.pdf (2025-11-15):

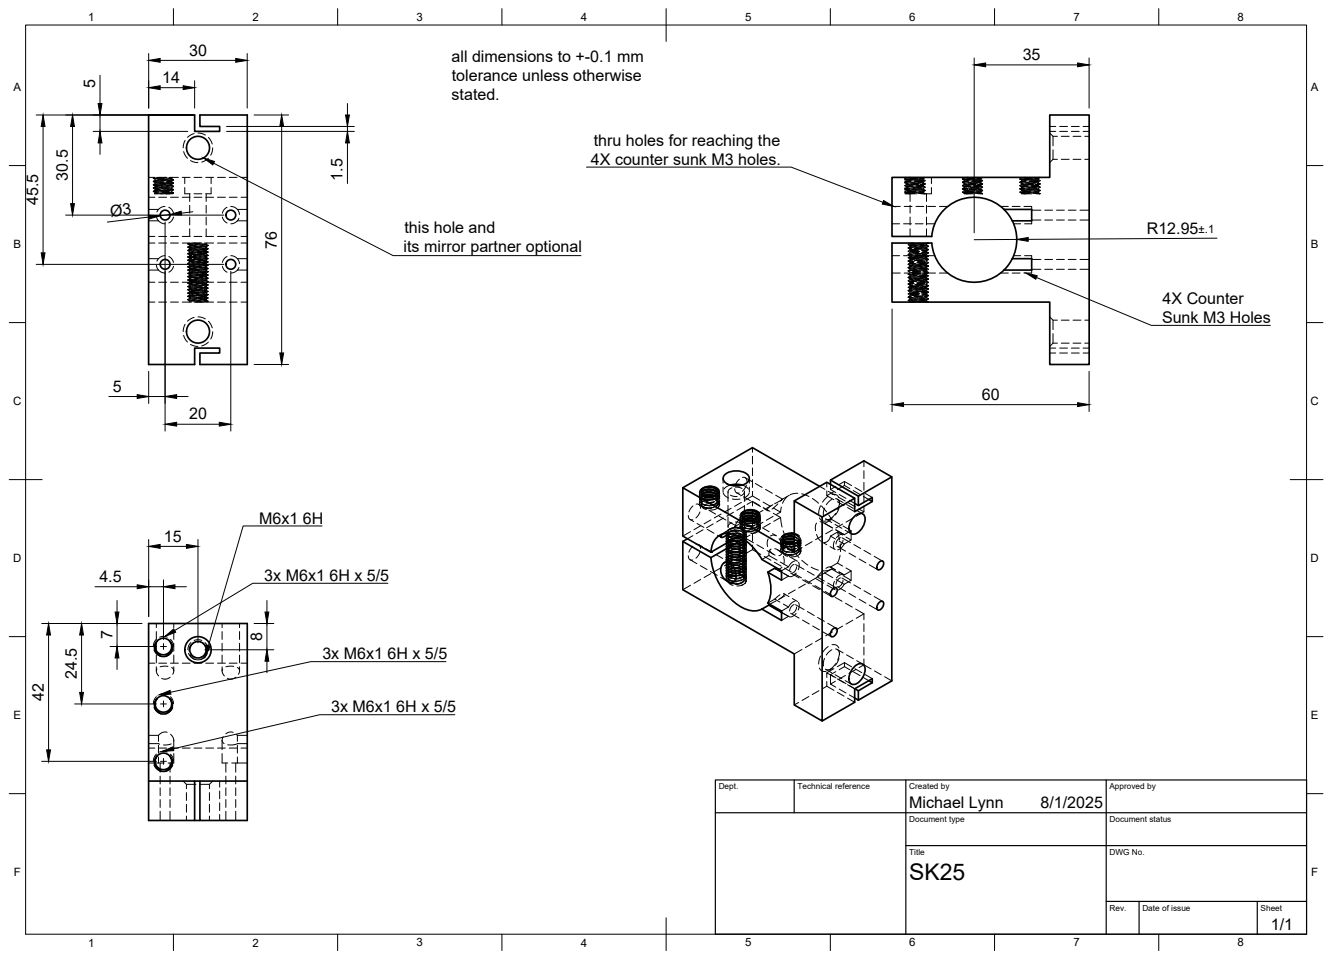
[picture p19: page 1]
Title; DWG No.; Rev.; Date of issue; Sheet; Michael Lynn 76; 4X Counter Sunk M3 Holes

all dimensions to +-0.1 mm
tolerance unless otherwise
stated.

thru holes for reaching the
4X counter sunk M3 holes.

this hole and
its mirror partner optional

Dept. | Technical reference | Created by 8/1/2025 | Approved by

Document type | Document status

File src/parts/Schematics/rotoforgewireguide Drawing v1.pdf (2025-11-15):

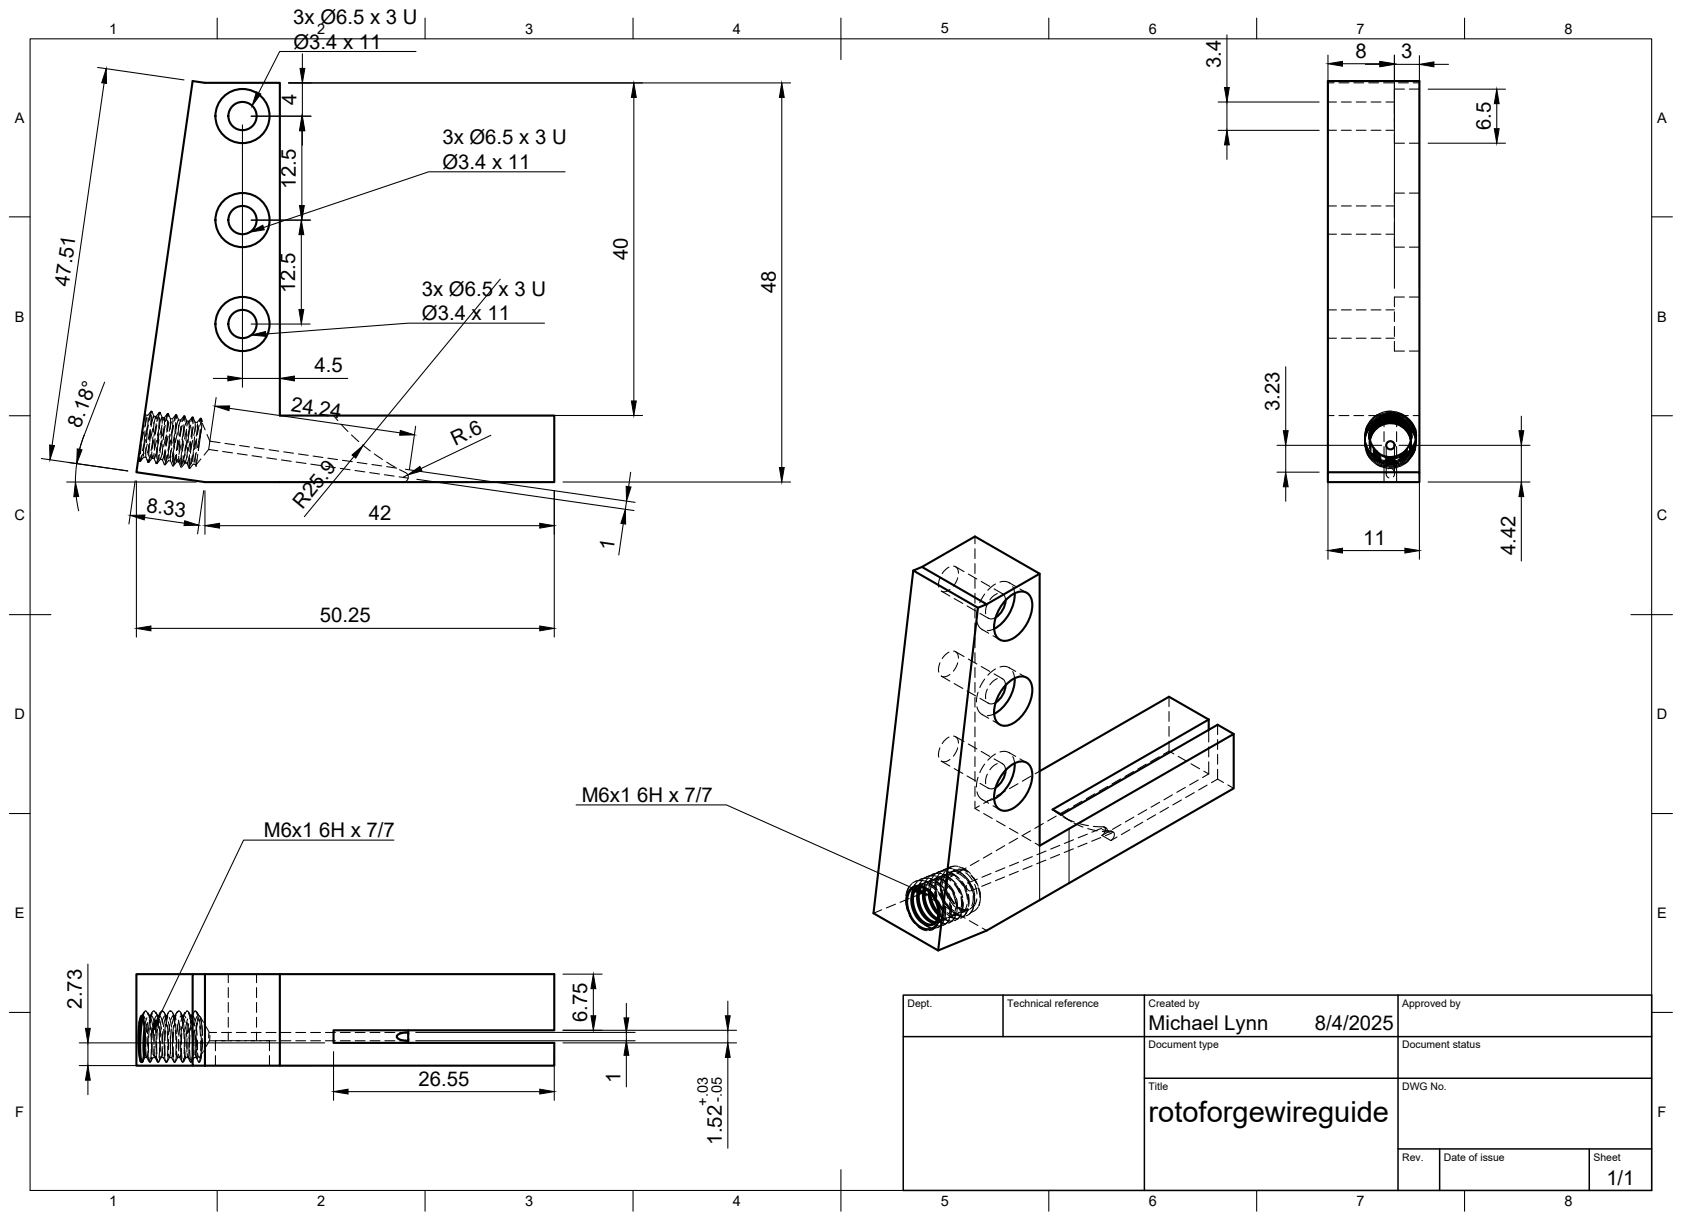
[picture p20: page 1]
Title; DWG No.; Rev.; Date of issue; Sheet

Dept. | Technical reference | Created by Michael Lynn 8/4/2025 | Approved by

Document type | Document status

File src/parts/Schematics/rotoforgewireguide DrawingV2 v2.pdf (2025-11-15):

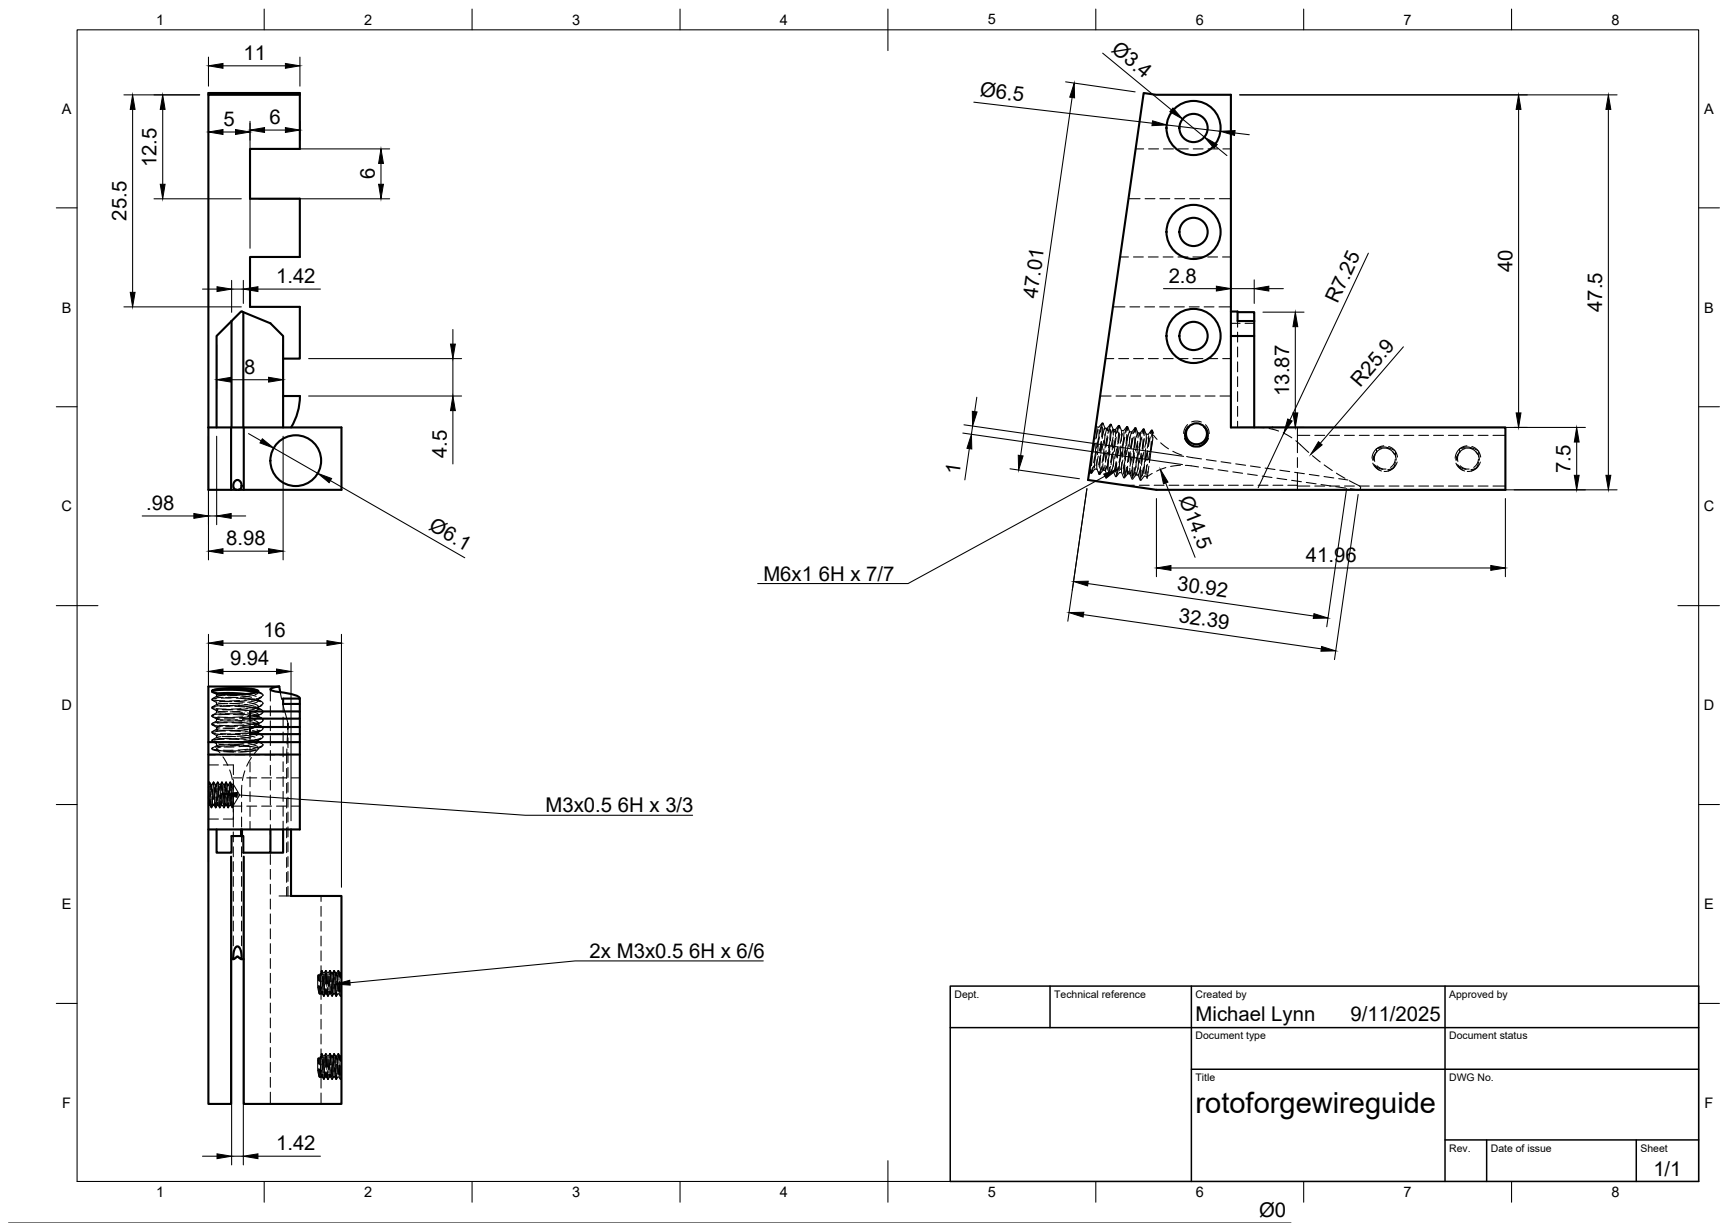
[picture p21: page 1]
Title; DWG No.; Rev.; Date of issue; Sheet

Dept. | Technical reference | Created by Michael Lynn 9/11/2025 | Approved by

Document type | Document status

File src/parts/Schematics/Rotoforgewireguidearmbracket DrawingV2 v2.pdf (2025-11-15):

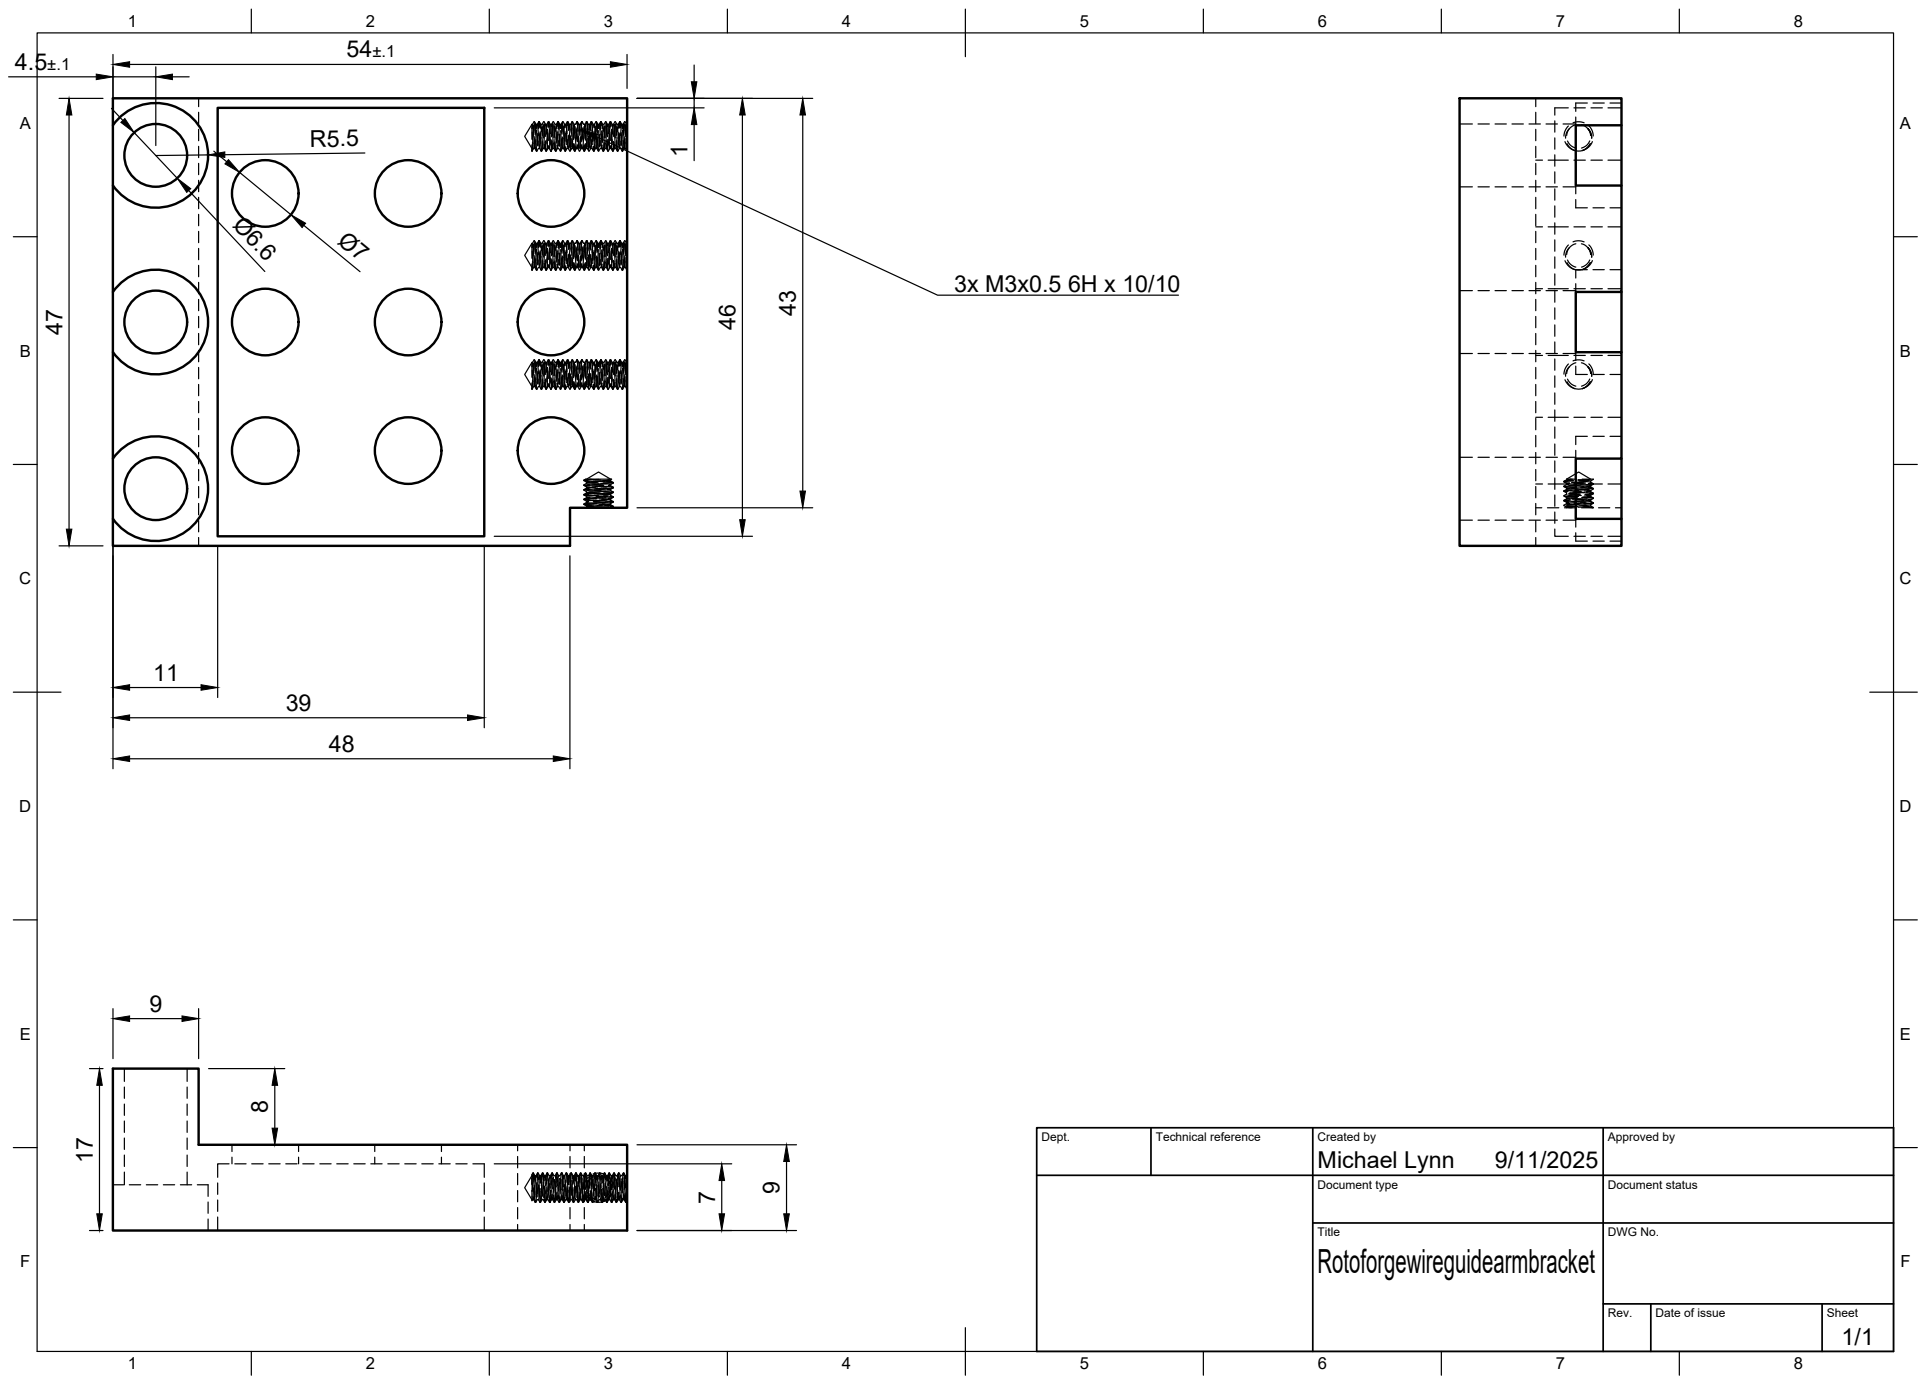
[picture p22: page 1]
Title; DWG No.; Rev.; Date of issue; Sheet; Michael Lynn 47

Dept. | Technical reference | Created by 9/11/2025 | Approved by

Document type | Document status

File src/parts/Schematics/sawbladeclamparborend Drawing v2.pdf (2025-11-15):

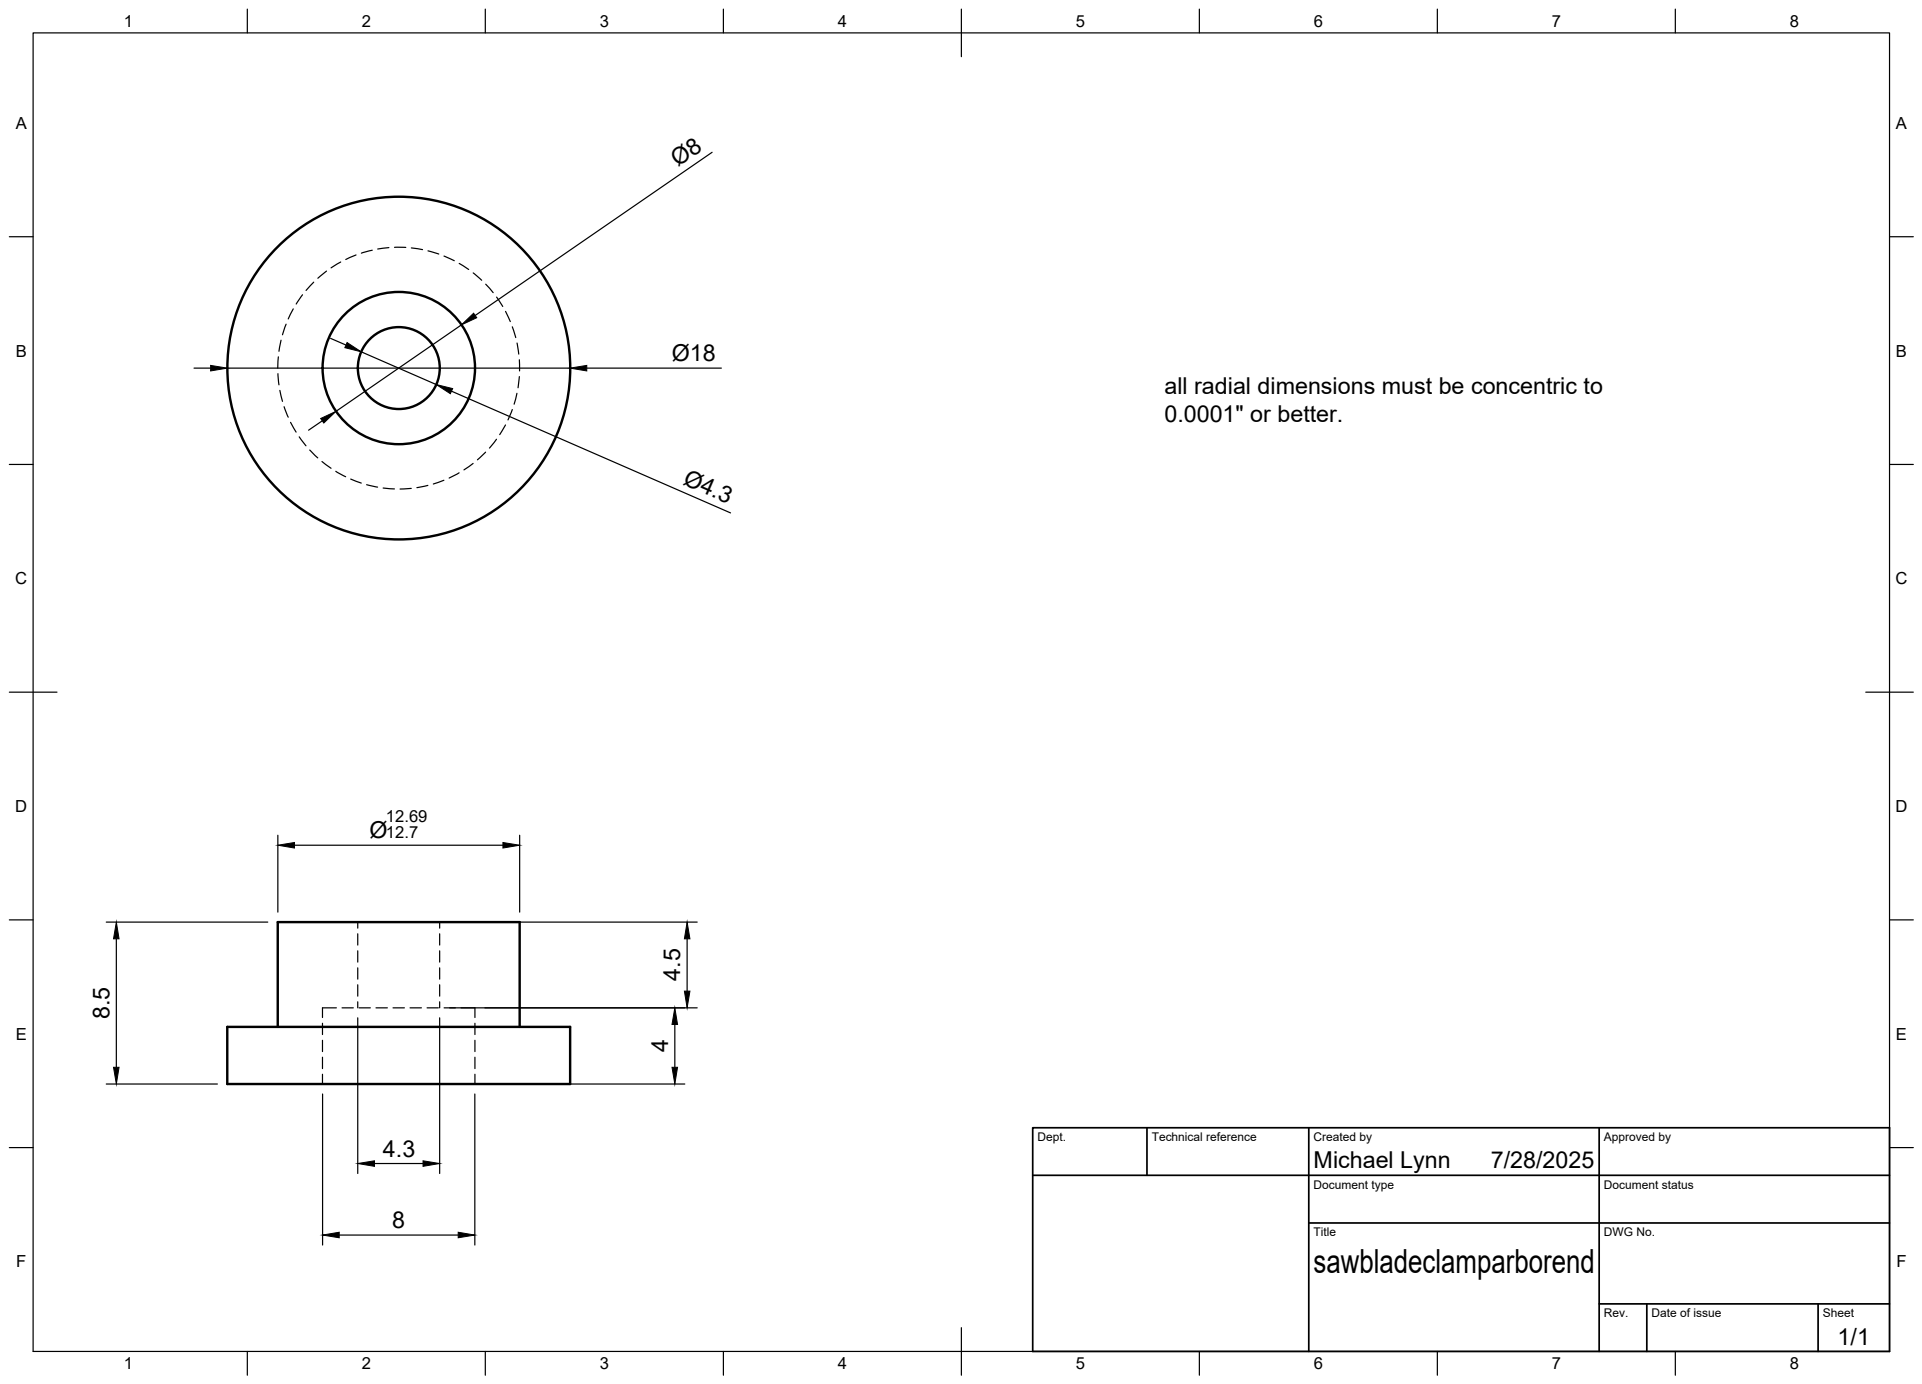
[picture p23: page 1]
Title; DWG No.; Rev.; Date of issue; Sheet

all radial dimensions must be concentric to
0.0001" or better.

Dept. | Technical reference | Created by Michael Lynn 7/28/2025 | Approved by

Document type | Document status

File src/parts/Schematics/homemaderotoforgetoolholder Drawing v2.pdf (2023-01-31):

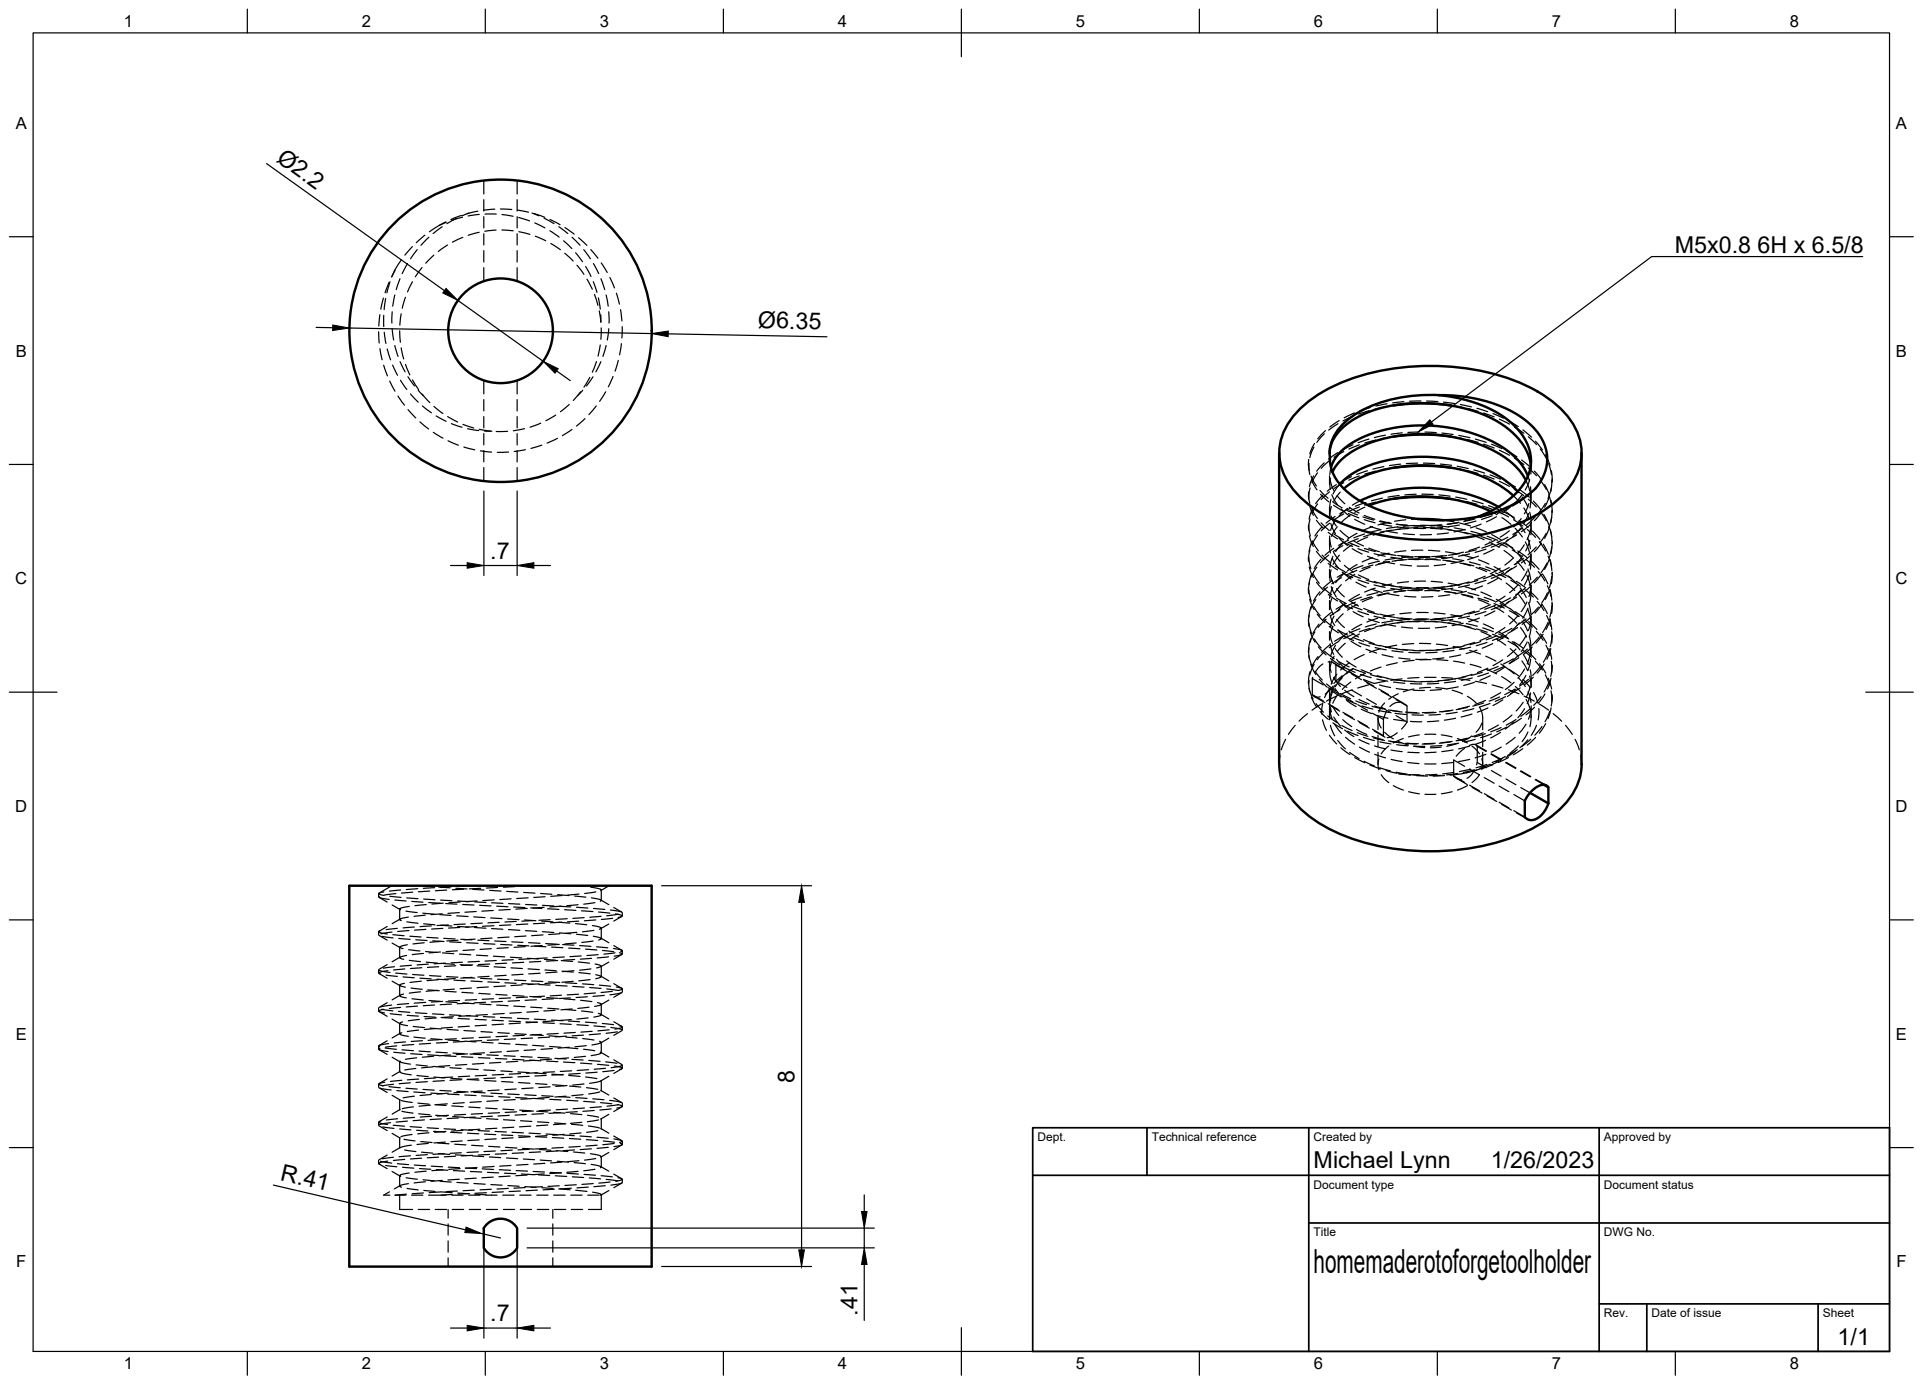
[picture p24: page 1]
Title; DWG No.; Rev.; Date of issue; Sheet

Dept. | Technical reference | Created by Michael Lynn 1/26/2023 | Approved by

Document type | Document status

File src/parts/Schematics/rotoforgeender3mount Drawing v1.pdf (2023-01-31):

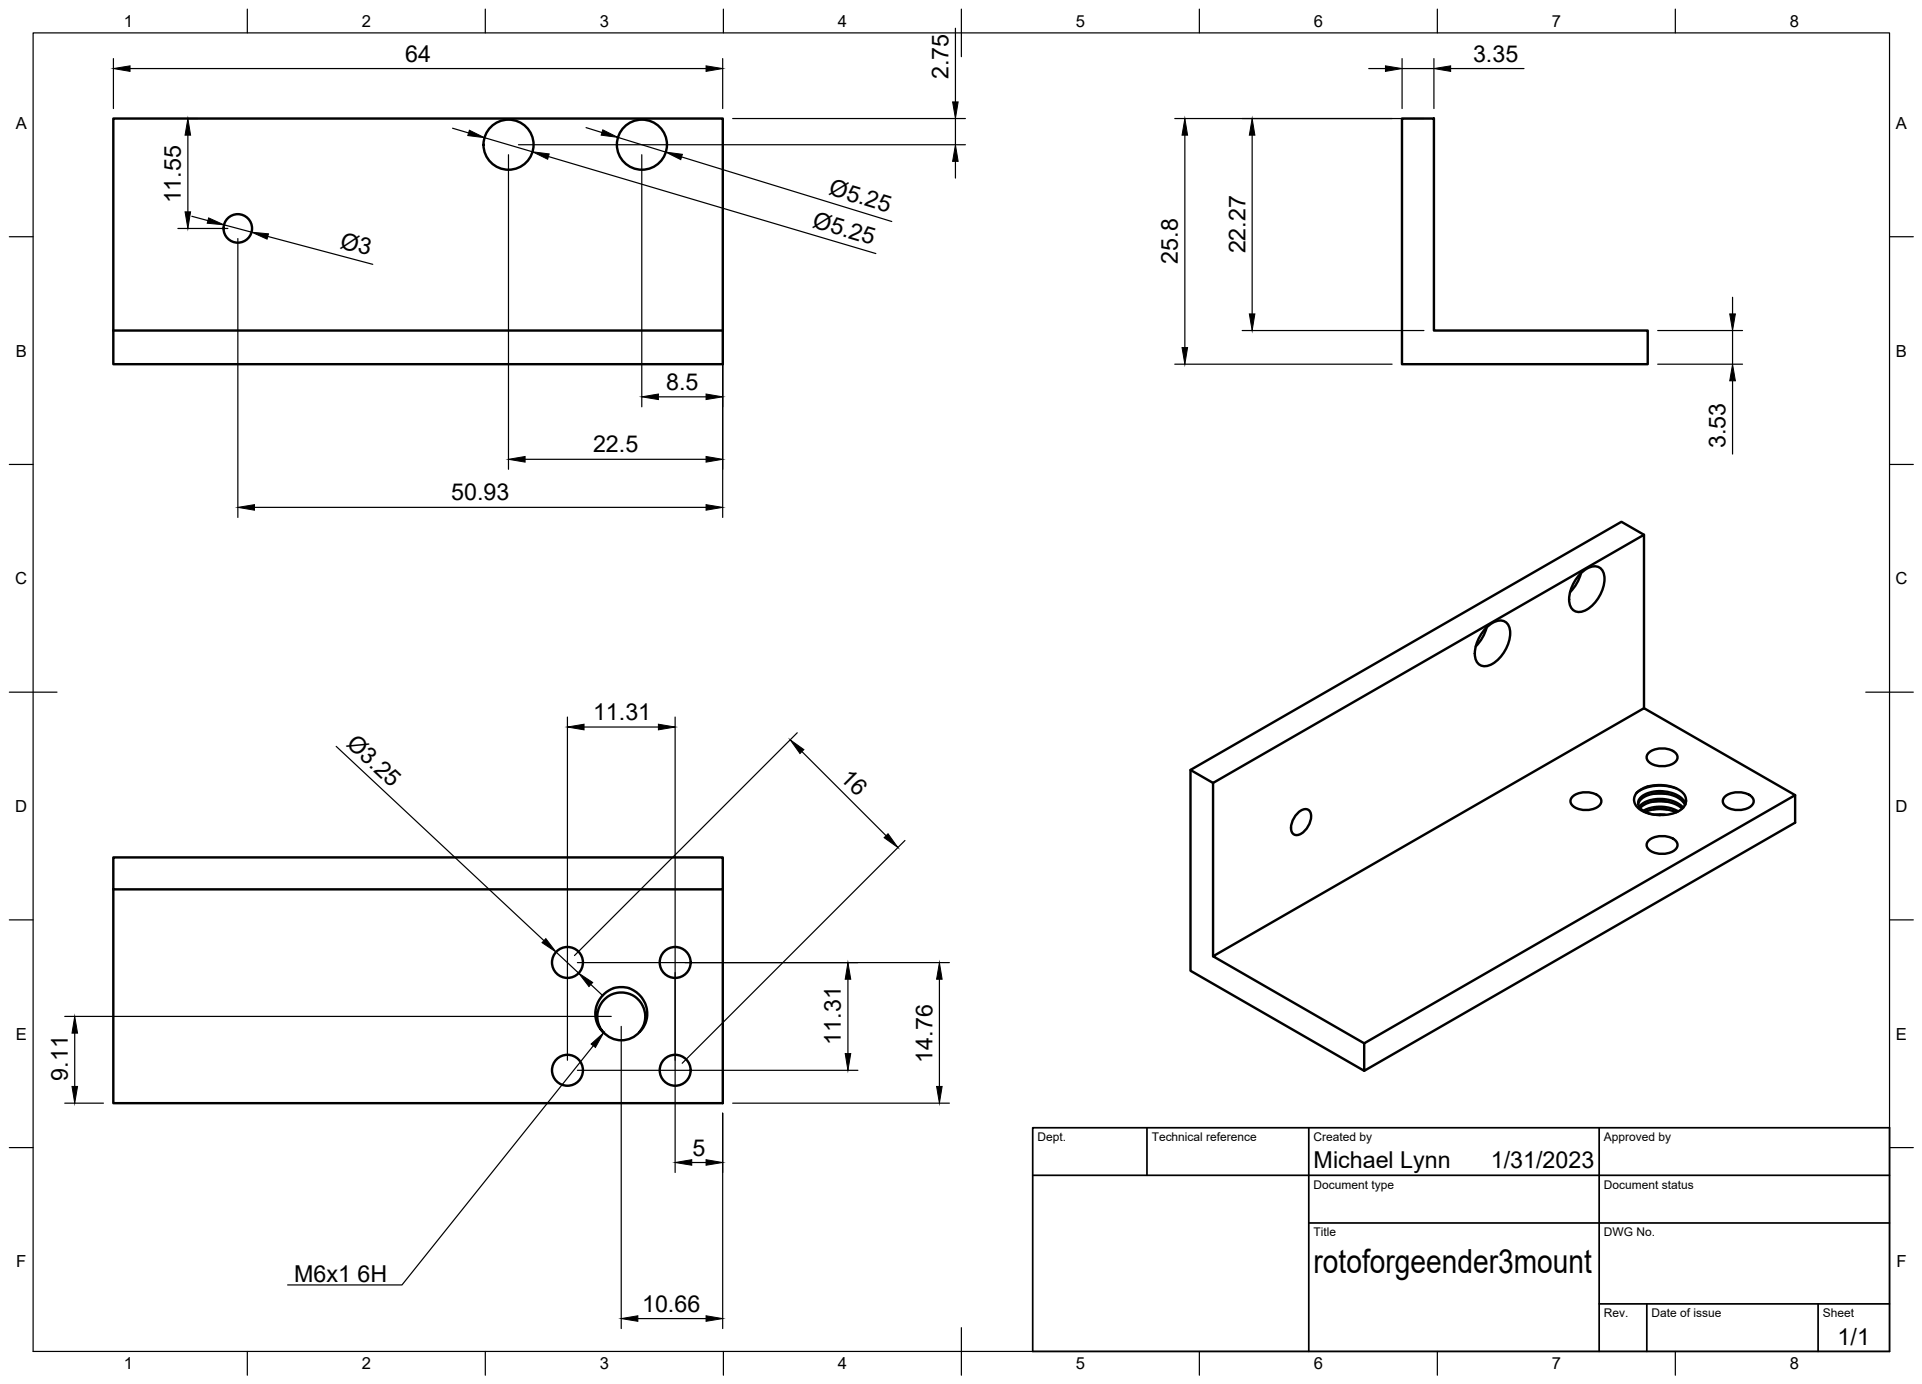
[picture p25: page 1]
Title; DWG No.; Rev.; Date of issue; Sheet

Dept. | Technical reference | Created by Michael Lynn 1/31/2023 | Approved by

Document type | Document status

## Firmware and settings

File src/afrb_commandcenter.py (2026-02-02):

import math
import tkinter as tk
from tkinter import ttk, filedialog, messagebox
import serial
import serial.tools.list_ports
import threading
import time
import csv
import datetime
import os

APP_TITLE = "AF-RB Control Center: Slicer + Monitor"

# ==========================================
# PART 1: SLICER HELPERS & GENERATORS (Preserved 100%)
# ==========================================

def parse_csv_floats(s):
    try:
        parts = [p.strip() for p in str(s).split(",") if p.strip() != ""]
        return [float(p) for p in parts] if parts else []
    except Exception:
        return []

def _is_fixture(P):
    return P.get('mode', 'bed') == 'fixture'

def _absZ(P, z):
    if _is_fixture(P) and P.get('fixture_apply_to_layers', False):
        return float(P.get('fixture_base_z', 0.0)) + float(z)
    return float(z)

def _approachZ(P):
    if _is_fixture(P):
        return float(P.get('fixture_base_z', 0.0)) + float(P.get('fixture_approach_z', 0.8))
    return _travelZ(P)

def _travelZ(P):
    tz = float(P.get('travel_z', 10.0))
    if _is_fixture(P) and P.get('fixture_apply_to_layers', False):
        return float(P.get('fixture_base_z', 0.0)) + tz
    return tz

def compute_e_per_mm(e_mode, bead_width, layer_height, wire_diam):
    if e_mode == "x":
        return 1.0
    wire_area = math.pi * (wire_diam/2.0)**2 if wire_diam > 0 else 0
    bead_area = bead_width * layer_height
    return bead_area / wire_area if wire_area > 0 else 1.0

def gcode_header(params):
    lines = []
    L = lines.append
    L("G90"); L("G21"); L("M83"); L("T0"); L("G92 E0")

    # Bed preheat
    bed = float(params.get('bed_temp', 0) or 0)
    wait_bed = bool(params.get('wait_bed', False))
    bed_dwell_ms = int(float(params.get('bed_dwell_ms', 0) or 0))
    if bed > 0:
        L(f"M140 S{int(bed)}")
        if wait_bed:
            L(f"M190 S{int(bed)}")
            if bed_dwell_ms > 0: L(f"G4 P{bed_dwell_ms}")
    else:
        L("M140 S0")

    # Hotend preheat
    hotend = max(0, min(280, int(float(params.get('hotend_temp', 0) or 0))))
    wait_he = bool(params.get('wait_hotend', False))
    he_dwell_ms = int(float(params.get('hotend_dwell_ms', 0) or 0))
    if hotend > 0:
        L(f"M104 S{hotend}")
        if wait_he:
            L(f"M109 S{hotend}")
            if he_dwell_ms > 0: L(f"G4 P{he_dwell_ms}")
    else:
        L("M104 S0")

    # Cold extrusion
    if bool(params.get('allow_cold_extrude', True)):
        L("M302 S0")
    else:
        min_e_temp = max(0, min(280, int(float(params.get('min_e_temp', 0) or 0))))
        if min_e_temp <= 0 and hotend > 0:
            min_e_temp = max(0, hotend - 20)
        L(f"M302 S{min_e_temp}")

    # Homing & environment
    L("G28")
    L(f"M106 S{int(params.get('fan', 0))}")
    L(f"M3 S{int(params.get('spindle', 30000))}")
    L("G4 P2000")

    # Mode-aware initial height
    if _is_fixture(params):
        L(f"G0 Z{_approachZ(params):.3f} F{int(params.get('feed_travel', 6000))}")
    else:
        L(f"G0 Z{_travelZ(params):.3f} F{int(params.get('feed_travel', 6000))}")
    return lines

def gcode_footer(params):
    return ["M5", "M107", f"G0 Z{_travelZ(params):.3f} F{int(params.get('feed_travel',6000))}"]

# --- GENERATORS (Copied Verbatim) ---

def gen_straight_multitrack(P):
    x_start = P['x_start']; y_start = P['y_start']; length_x = P['length_x']
    z_first = P['z_first']; z_step = P['z_step']; z_final = P['z_final']
    feed_dep = P['feed_dep']; feed_z = P['feed_z']; feed_travel = P['feed_travel']
    dwell_ms = P['dwell_ms']
    e_mode = P['e_mode']; bead_width = P['bead_width']; wire_diam = P['wire_diam']
    lead_in = P['lead_in']; runout = P['runout']; retract = P['retract']
    use_z_dive_cut = P['use_z_dive_cut']; z_dive_amount = P['z_dive_amount']
    multitrack = P['multitrack']; track_count = max(1, int(P['track_count'])); overlap_frac = max(0.0, min(0.9, P['overlap_frac']))
    serpentine_y = P['serpentine_y']

    x_end = x_start - length_x
    x_lead_in_start = x_start + max(0.0, lead_in)
    x_end_runout = x_end - max(0.0, runout)

    e_per_mm = compute_e_per_mm(e_mode, bead_width, z_step, wire_diam)
    spacing = bead_width * (1.0 - overlap_frac)
    y_tracks_up = [y_start + i * spacing for i in range(track_count)]

    lines = []
    lines += gcode_header(P)

    first_move_done = False
    z = z_first; layer_idx = 0
    while z <= z_final + 1e-9:
        z_abs = _absZ(P, z)
        y_list = y_tracks_up if (layer_idx % 2 == 0 or not serpentine_y) else list(reversed(y_tracks_up))
        for y in y_list:
            z_move = _approachZ(P) if (not first_move_done and P.get('fixture_first_move_at_approach', True) and _is_fixture(P)) else _travelZ(P)
            lines.append(f"G0 X{x_lead_in_start:.3f} Y{y:.3f} Z{z_move:.3f} F{int(feed_travel)}")
            first_move_done = True
            lines.append(f"G1 Z{z_abs:.3f} F{int(feed_z)}")
            if dwell_ms > 0: lines.append(f"G4 P{int(dwell_ms)}")
            if lead_in > 0: lines.append(f"G1 X{x_start:.3f} F{int(feed_dep)}")
            E = e_per_mm * (x_start - x_end)
            lines.append(f"G1 X{x_end:.3f} E{E:.3f} F{int(feed_dep)}")
            if runout > 0: lines.append(f"G1 X{x_end_runout:.3f} F{int(feed_dep)}")
            if use_z_dive_cut and z_dive_amount > 0:
                lines += ["G91", f"G1 Z{-abs(z_dive_amount):.3f} F{int(feed_z)}", "G90"]
            if retract != 0: lines.append(f"G1 E{-abs(retract):.3f} F600")
            lines.append(f"G0 Z{_travelZ(P):.3f} F{int(feed_travel)}")
            lines.append("G92 E0")
        z += z_step; layer_idx += 1

    lines += gcode_footer(P)
    return "\n".join(lines)

def gen_dot_stack(P):
    x = P['x_start']; y = P['y_start']
    z_first = P['z_first']; z_step = P['z_step']; z_final = P['z_final']
    feed_dep = P['feed_dep']; feed_z = P['feed_z']; feed_travel = P['feed_travel']
    dwell_ms = P['dwell_ms']; e_pulse = P['e_pulse']; e_retract = P['e_retract']

    lines = []; lines += gcode_header(P)
    first_move_done = False

    z = z_first
    while z <= z_final + 1e-9:
        z_abs = _absZ(P, z)
        z_move = _approachZ(P) if (not first_move_done and P.get('fixture_first_move_at_approach', True) and _is_fixture(P)) else _travelZ(P)
        lines.append(f"G0 X{x:.3f} Y{y:.3f} Z{z_move:.3f} F{int(feed_travel)}")
        first_move_done = True
        lines.append(f"G1 Z{z_abs:.3f} F{int(feed_z)}")
        if dwell_ms > 0: lines.append(f"G4 P{int(dwell_ms)}")
        lines.append(f"G1 E{e_pulse:.3f} F{int(feed_dep)}")
        if e_retract != 0: lines.append(f"G1 E{-abs(e_retract):.3f} F600")
        lines.append(f"G0 Z{_travelZ(P):.3f} F{int(feed_travel)}")
        lines.append("G92 E0")
        z += z_step
    lines += gcode_footer(P)
    return "\n".join(lines)

def gen_sideways_micro_raster(P):
    x_start = P['x_start']; y0 = P['y_start']; x_stroke = P['x_stroke']
    y_span = P['y_span']; dy = max(0.01, P['dy_step'])
    z_first = P['z_first']; z_step = P['z_step']; z_final = P['z_final']
    feed_dep = P['feed_dep']; feed_z = P['feed_z']; feed_travel = P['feed_travel']
    dwell_ms = P['dwell_ms']; runout = P['runout']; retract = P['retract']
    e_mode = P['e_mode']; bead_width = P['bead_width']; wire_diam = P['wire_diam']

    x_end = x_start - x_stroke
    x_end_runout = x_end - max(0.0, runout)
    e_per = compute_e_per_mm(e_mode, bead_width, z_step, wire_diam) * x_stroke
    n_tracks = max(1, int(math.ceil(y_span / dy)))

    lines = []; lines += gcode_header(P)
    first_move_done = False

    z = z_first
    while z <= z_final + 1e-9:
        z_abs = _absZ(P, z)
        y = y0
        for _ in range(n_tracks):
            z_move = _approachZ(P) if (not first_move_done and P.get('fixture_first_move_at_approach', True) and _is_fixture(P)) else _travelZ(P)
            lines.append(f"G0 X{x_start:.3f} Y{y:.3f} Z{z_move:.3f} F{int(feed_travel)}")
            first_move_done = True
            lines.append(f"G1 Z{z_abs:.3f} F{int(feed_z)}")
            if dwell_ms > 0: lines.append(f"G4 P{int(dwell_ms)}")
            lines.append(f"G1 X{x_end:.3f} E{e_per:.3f} F{int(feed_dep)}")
            if runout > 0: lines.append(f"G1 X{x_end_runout:.3f} F{int(feed_dep)}")
            if retract != 0: lines.append(f"G1 E{-abs(retract):.3f} F600")
            lines.append(f"G0 Z{_travelZ(P):.3f} F{int(feed_travel)}")
            lines.append("G92 E0")
            y += dy
        z += z_step
    lines += gcode_footer(P)
    return "\n".join(lines)

def gen_diagonal_drift(P):
    x_start = P['x_start']; y_start = P['y_start']; x_total = P['x_total']
    y_drift = P['y_drift']; seg_dx = max(0.01, P['seg_dx'])
    z_first = P['z_first']; z_step = P['z_step']; z_final = P['z_final']
    feed_dep = P['feed_dep']; feed_z = P['feed_z']; feed_travel = P['feed_travel']
    dwell_ms = P['dwell_ms']; runout = P['runout']; retract = P['retract']
    e_mode = P['e_mode']; bead_width = P['bead_width']; wire_diam = P['wire_diam']

    n_segments = max(1, int(round(x_total / seg_dx)))
    dx = x_total / n_segments; dy = y_drift / n_segments

    lines = []; lines += gcode_header(P)
    first_move_done = False

    z = z_first
    while z <= z_final + 1e-9:
        z_abs = _absZ(P, z)
        z_move = _approachZ(P) if (not first_move_done and P.get('fixture_first_move_at_approach', True) and _is_fixture(P)) else _travelZ(P)
        lines.append(f"G0 X{x_start:.3f} Y{y_start:.3f} Z{z_move:.3f} F{int(feed_travel)}")
        first_move_done = True
        lines.append(f"G1 Z{z_abs:.3f} F{int(feed_z)}")
        if dwell_ms > 0: lines.append(f"G4 P{int(dwell_ms)}")
        x = x_start; y = y_start
        e_per_seg = compute_e_per_mm(e_mode, bead_width, z_step, wire_diam) * abs(dx)
        for _ in range(n_segments):
            x -= dx; y += dy
            if dx >= 0:  # must be negative X
                continue
            lines.append(f"G1 X{x:.3f} Y{y:.3f} E{e_per_seg:.3f} F{int(feed_dep)}")
        if runout > 0: lines.append(f"G1 X{(x - runout):.3f} F{int(feed_dep)}")
        if retract != 0: lines.append(f"G1 E{-abs(retract):.3f} F600")
        lines.append(f"G0 Z{_travelZ(P):.3f} F{int(feed_travel)}")
        lines.append(f"G0 X{x_start:.3f} Y{y_start:.3f} F{int(feed_travel)}")
        lines.append("G92 E0")
        z += z_step
    lines += gcode_footer(P)
    return "\n".join(lines)

def gen_overhang_tests(P):
    x_start = P['x_start']; y_base = P['y_base']; length_x = P['length_x']
    z_first = P['z_first']; z_offsets = parse_csv_floats(P['z_offsets_csv']) or [0.10,0.20,0.30,0.40,0.50]
    y_list = parse_csv_floats(P['y_offsets_csv'])
    if not y_list:
        step = float(P['y_step'])
        y_list = [i * step for i in range(len(z_offsets))]

    n = min(len(z_offsets), len(y_list))
    z_offsets = z_offsets[:n]; y_list = y_list[:n]
    x_end = x_start - length_x
    e_per_mm = compute_e_per_mm(P['e_mode'], P['bead_width'], P['layer_height'], P['wire_diam'])
    feed_dep = P['feed_dep']; feed_z = P['feed_z']; feed_travel = P['feed_travel']
    dwell_ms = P['dwell_ms']; runout = P['runout']; retract = P['retract']

    lines = []; lines += gcode_header(P)
    first_move_done = False

    for i in range(n):
        z = z_first + z_offsets[i]
        z_abs = _absZ(P, z)
        y = y_base + y_list[i]
        z_move = _approachZ(P) if (not first_move_done and P.get('fixture_first_move_at_approach', True) and _is_fixture(P)) else _travelZ(P)
        lines.append(f"G0 X{x_start:.3f} Y{y:.3f} Z{z_move:.3f} F{int(feed_travel)}")
        first_move_done = True
        lines.append(f"G1 Z{z_abs:.3f} F{int(feed_z)}")
        if dwell_ms > 0: lines.append(f"G4 P{int(dwell_ms)}")
        E = e_per_mm * (x_start - x_end)
        lines.append(f"G1 X{x_end:.3f} E{E:.3f} F{int(feed_dep)}")
        if runout > 0: lines.append(f"G1 X{(x_end - runout):.3f} F{int(feed_dep)}")
        if retract != 0: lines.append(f"G1 E{-abs(retract):.3f} F600")
        lines.append(f"G0 Z{_travelZ(P):.3f} F{int(feed_travel)}")
        lines.append("G92 E0")
    lines += gcode_footer(P)
    return "\n".join(lines)

# ==========================================
# PART 2: NEW MONITOR GAUGE
# ==========================================

class SpeedometerGauge(tk.Canvas):
    def __init__(self, parent, width=300, height=180, max_value=30000, **kwargs):
        super().__init__(parent, width=width, height=height, **kwargs)
        self.width = width
        self.height = height
        self.max_value = max_value
        self.center_x = width / 2
        self.center_y = height - 20 
        self.radius = min(width/2, height) - 20
        self.draw_background()
        self.needle = self.create_line(self.center_x, self.center_y, self.center_x, self.center_y - self.radius, fill="red", width=4, arrow=tk.LAST)
        self.value_text = self.create_text(self.center_x, self.center_y - 40, text="0 RPM", font=("Arial", 14, "bold"), fill="#333")

    def draw_background(self):
        # Zones: Green (0-20k), Yellow (20k-25k), Red (25k-30k)
        self.create_arc(20, 20+self.height-self.radius, self.width-20, self.center_y + self.radius, start=0, extent=30, style=tk.ARC, outline="red", width=20)
        self.create_arc(20, 20+self.height-self.radius, self.width-20, self.center_y + self.radius, start=30, extent=30, style=tk.ARC, outline="gold", width=20)
        self.create_arc(20, 20+self.height-self.radius, self.width-20, self.center_y + self.radius, start=60, extent=120, style=tk.ARC, outline="#4CAF50", width=20)
        
        # Ticks
        for i in range(0, 31, 5):
            angle = 180 - (i * 1000 / self.max_value) * 180
            rad = math.radians(angle)
            r1 = self.radius - 10; r2 = self.radius + 5
            x1 = self.center_x + r1 * math.cos(rad); y1 = self.center_y - r1 * math.sin(rad)
            x2 = self.center_x + r2 * math.cos(rad); y2 = self.center_y - r2 * math.sin(rad)
            self.create_line(x1, y1, x2, y2, fill="#333", width=2)
            
            # Text
            tr = self.radius - 25
            tx = self.center_x + tr * math.cos(rad); ty = self.center_y - tr * math.sin(rad)
            self.create_text(tx, ty, text=str(i), font=("Arial", 8))

    def set_value(self, rpm):
        rpm = max(0, min(rpm, self.max_value))
        angle = 180 - (rpm / self.max_value) * 180
        rad = math.radians(angle)
        nr = self.radius - 15
        nx = self.center_x + nr * math.cos(rad)
        ny = self.center_y - nr * math.sin(rad)
        self.coords(self.needle, self.center_x, self.center_y, nx, ny)
        self.itemconfigure(self.value_text, text=f"{int(rpm)} RPM")

# ==========================================
# PART 3: MAIN APP (INTEGRATED)
# ==========================================
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

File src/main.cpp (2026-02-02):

/*
 * ESP32 Robust Tachometer (Burst Median Filter)
 * * Function: Captures 9 consecutive pulses, sorts them, and reports the median.
 * * Latency: ~18ms at 30k RPM.
 */

#include <Arduino.h>
#include <vector>
#include <algorithm> // Required for sorting

// --- Configuration ---
const int TACH_PIN = 27;       
const int VOLT_PIN = 34;       
const int PULSES_PER_REV = 1;  
const float DIVIDER_RATIO = 1; 

// --- Variables ---
volatile unsigned long lastPulseTime = 0;
volatile unsigned long pulseInterval = 0;
volatile bool newData = false;

// Interrupt Service Routine (Fast)
void IRAM_ATTR handleTachPulse() {
  unsigned long currentTime = esp_timer_get_time();
  // Hardware Debounce: Ignore noise faster than 40,000 RPM (1500us)
  if ((currentTime - lastPulseTime) > 1500) { 
    pulseInterval = currentTime - lastPulseTime;
    lastPulseTime = currentTime;
    newData = true;
  }
}

// Helper: Calculate Median
int getMedian(std::vector<int> val) {
  std::sort(val.begin(), val.end());
  return val[val.size() / 2]; // Return the middle element
}

void setup() {
  Serial.begin(115200);
  pinMode(TACH_PIN, INPUT);
  pinMode(VOLT_PIN, INPUT);
  
  analogReadResolution(12);
  analogSetAttenuation(ADC_11db); 

  attachInterrupt(digitalPinToInterrupt(TACH_PIN), handleTachPulse, RISING);
  Serial.println("START"); 
}

void loop() {
  // 1. Collect Burst of 9 Samples
  std::vector<int> rpmSamples;
  int samplesNeeded = 9; 

  // Timeout safety: Give up if collection takes too long (e.g. motor stopped)
  unsigned long startBurst = millis();
  
  while(rpmSamples.size() < samplesNeeded && (millis() - startBurst < 200)) {
    
    // Check for "Stopped" motor (No pulse for 0.5s)
    if (esp_timer_get_time() - lastPulseTime > 500000) {
       // Fill remaining samples with 0 to force the median down quickly
       while(rpmSamples.size() < samplesNeeded) rpmSamples.push_back(0);
       break;
    }

    // Capture Pulse
    if (newData) {
      noInterrupts();
      unsigned long interval = pulseInterval;
      newData = false; // Reset flag
      interrupts();

      if (interval > 0) {
        // Calculate RPM instantly
        int r = (int)(1000000.0 / interval * 60.0 / PULSES_PER_REV);
        rpmSamples.push_back(r);
      }
    }
    // NO DELAY HERE: We want to catch the very next pulse immediately.
  }

  // 2. Calculate Median RPM
  int finalRPM = 0;
  if (rpmSamples.size() > 0) {
    finalRPM = getMedian(rpmSamples);
  }

  // 3. Read Voltage (Quick Average)
  long adcSum = 0;
  for(int i=0; i<10; i++) {
    adcSum += analogRead(VOLT_PIN);
    delayMicroseconds(10);
  }
  float voltage = (adcSum / 10.0 / 4095.0) * 3.3 * DIVIDER_RATIO;

  // 4. Output to Serial
  Serial.print(millis());
  Serial.print(",");
  Serial.print(voltage, 2); 
  Serial.print(",");
  Serial.println(finalRPM);
  
  // Optional: Main loop delay to control CSV file size
  // delay(50); 
}

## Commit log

2023-01-24 Add files via upload
    added all the details of the basic bill of materials for the project... the readme and contribution guidelines need to be updated next... probably along with relevant CAD and CAM documentation to sho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
    [billofmaterials.xlsx]
2023-01-31 Added src and docs folders...added detailed moldels of hardware components, added beginning of a literature review and a completed bill of materials.
    there should be everything in here required for someone to replicate the rotoforge project. its not perfectly organized yet so I am happy to provide some help to the intrepid explorers interested in 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
    [#Fitting_PC4-M6 v1.f3d, #Fitting_PC4-M6 v1.step, M5acronnuterotoforgetool v1.f3d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]
2024-08-10 added folder for untested designs, and files for tiny power hammer and overkill extruder
    [in progress extruder.step]
2024-08-10 added BOM for current ovekill wire extruder design
    [off the shelf parts.csv]
2024-08-11 updated BOM for overkill extruder, updated ToDo files, got overkill ready for full printed test, not ready to order machined rollers and lazer cut gears and off the shelf parts yet.
    [in progress extruder.step, off the shelf parts.csv, overkill extruder--ready for full 3d printed test.step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]
2024-08-11 improved skrew acess
    [Overkill Extruder.step, overkill extruder--ready for full 3d printed test.step, overkill extruder--ready for fully printed test.3mf]
2024-08-11 fixed tensioner gear shaft clearance
    [Overkill Extruder.step]
2024-08-13 added orbital friction design
    [off the shelf parts.csv, orbital friction print head.step]
2024-08-16 improved extruder design tensioning mechanism. changed to more readily available bearings for orbital friction approack, updated both BOMs
    [BOM.csv, Orbital Friction Full Assy.step, Overkill Extruder v4.step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]
2024-08-25 added code for extrider quick test
    [BOM.csv]
2024-11-13 added bldc controller to test code for orbital
    [BOM.csv]
2024-11-13 added bldc motor tesion slot, and hole to mount a mechanism to rotationally stabalize the die
2024-11-23 added top wire support for overkill extruder
    [Overkill Extruder- AP242.step]
2025-11-15 Update README.md
    condensed and simplified readme. Added more conceptual links, and generalized the description to fit friction rolling, but also other friction welding approaches.
2025-11-15 Add files via upload
    a simple tkinter gui based python app for generating valid g-code paths for Rotoforge.
    I have successfully used this app to print one line thick walls in X and Y, up to 10 mm height, with good mechanical properties.
    Printed test coupons in Aluminum-1100 and 5054, and demonstrated basic overhang, and tested bonding of parallel lines to each other laterally.
2025-11-15 added some basic images, deprecated old designs, and added new cad and schematics and code.
2025-11-15 added schematics for latest rotoforge version AFRB with sawbladesand arbors
2025-11-15 added new model files to parts src
    [3044A65_Smooth-Finish Slitting Saw v1.f3d, 3044A65_Smooth-Finish Slitting Saw v1.step, RotoforgeArbor v4.f3d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]
2025-11-15 addedversion1 parts to deprecated folder.
    [#Fitting_PC4-M6 v1.f3d, #Fitting_PC4-M6 v1.step, M5acronnuterotoforgetool v1.f3d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]
2025-11-15 added sample and data images
    deposit pictures, tensile and 4pt bend flexural data as well as priting downforce data images.
2025-11-16 removed old stuff
    [billofmaterials.xlsx]
2025-11-16 edited links in BOM
    [Rotoforge BOM 11152025 - Amazon BOM(1).csv, Rotoforge BOM 11152025(2).ods, Rotoforge BOM 11152025.ods]
2026-01-18 Modified AFRB script to include logging functions in a separate tab. Added main.cpp and platformio.ini for esp32 used for microcontroller for logging motor data to CSV file. Added example logging out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
    [motor_log_2026-01-10_19-09-15.csv]
